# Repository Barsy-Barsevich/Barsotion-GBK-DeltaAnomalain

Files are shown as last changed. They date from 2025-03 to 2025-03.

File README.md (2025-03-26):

# Barsotion GBK DeltaAnomalain
Board computer for OKB Iva "Kilka" rocket, 2024

## Parameters
- Microcontroller: LGT8X328P
- Clock frequency: 32MHz
- Gyroscope: on-board MPU6050 (I2C)
- Barometer: external, 2x BMP388 (I2C)
- Memory: 8MB SPI NOR Flash

The clock frequency is 32 MHz provided by design, however before the flight 07.07.2024 we need to reduce it to 16 MHz, unless the computer was unstable in working.

## Software
- [DeltaAnomalain flight software](https://github.com/Barsy-Barsevich/KILKA_Soft)

## Continious progress
- [Previous version: Barsotion GBK GammaAnomalain](https://github.com/Barsy-Barsevich/Barsotion-GBK-GammaAnomalain)
- [Next version: Barsotion-EA (GBK EpsilonAnomalain](https://github.com/Barsy-Barsevich/Barsotion-EA)

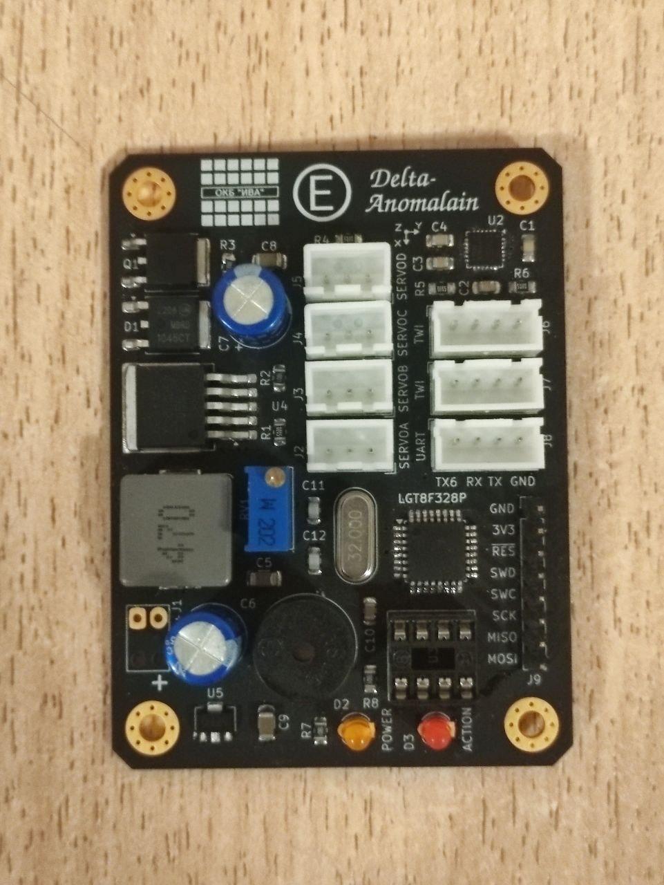
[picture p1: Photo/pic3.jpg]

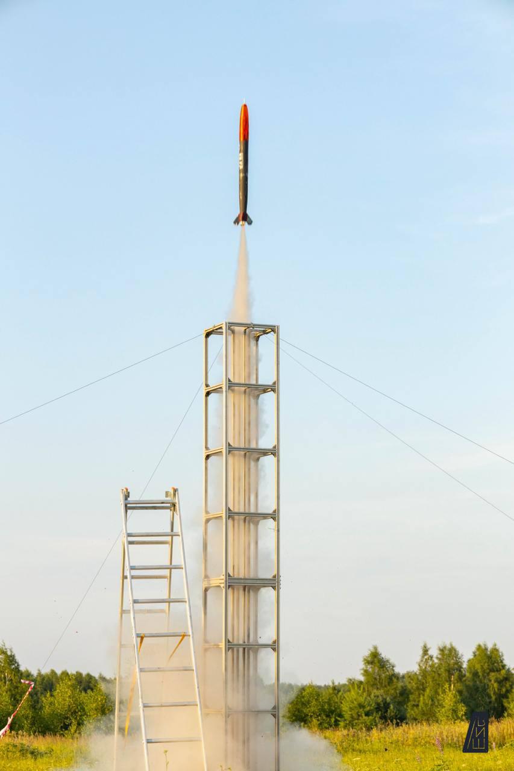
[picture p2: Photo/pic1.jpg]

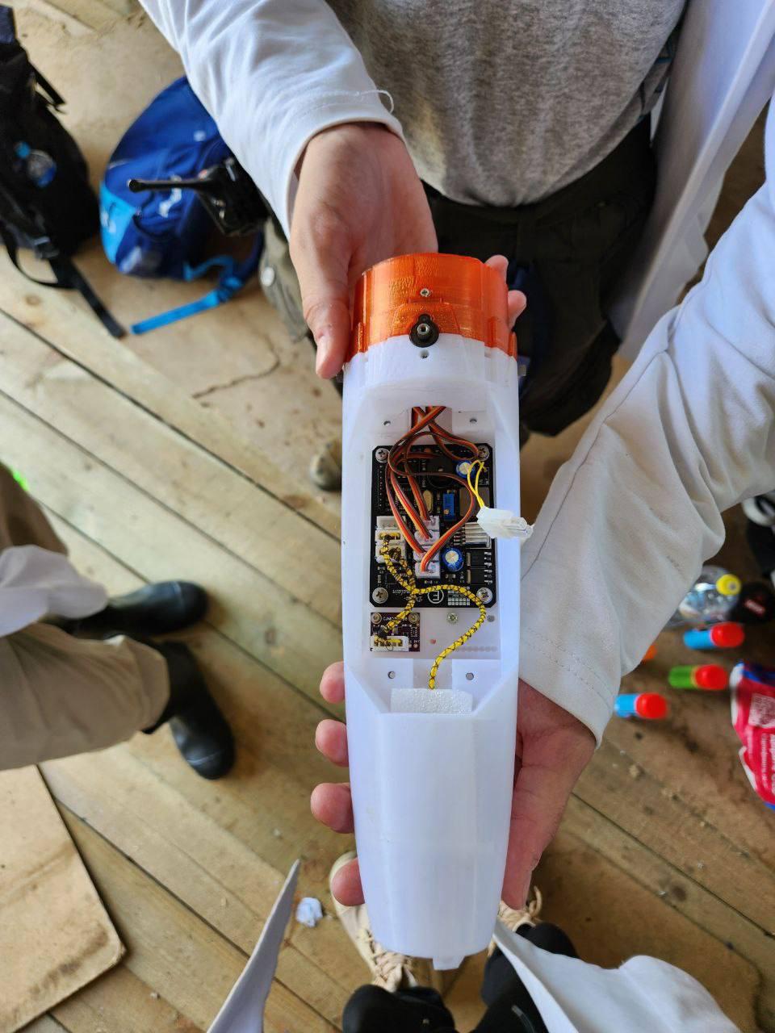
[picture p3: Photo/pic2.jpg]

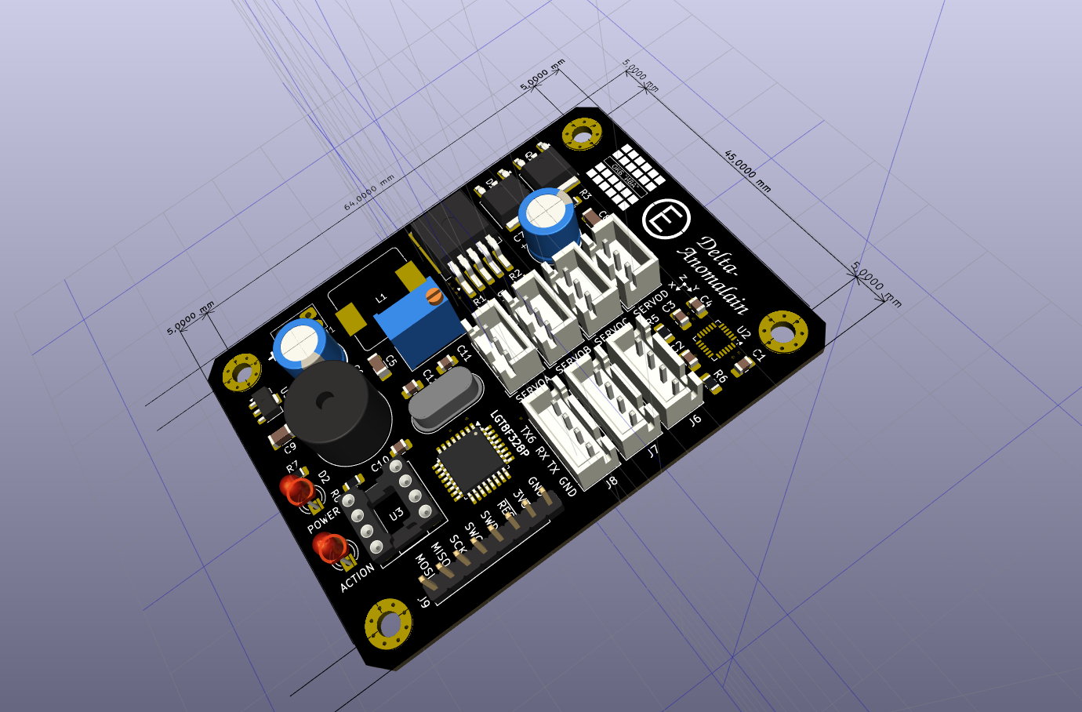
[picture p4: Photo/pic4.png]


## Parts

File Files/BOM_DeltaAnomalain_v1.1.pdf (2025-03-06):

Reference | Value | Footprint | Qty | Description
BZ1 | Buzzer | Buzzer_Beeper:MagneticBuzzer_ProSignal_ABI-009-RC | 1 Buzzer, polarized
C1 | 2.2nF | Capacitor_SMD:C_0805_2012Metric_Pad1.18x1.45mm_HandSolder | 1 Unpolarized capacitor
C2,C3 | 100nF | Capacitor_SMD:C_0805_2012Metric_Pad1.18x1.45mm_HandSolder | 2 Unpolarized capacitor
C4,C10 | 10nF | Capacitor_SMD:C_0805_2012Metric_Pad1.18x1.45mm_HandSolder | 2 Unpolarized capacitor
C5,C8,C9 | 1uF | Capacitor_SMD:C_1206_3216Metric | 3 Unpolarized capacitor
C6,C7 | 470uF | Capacitor_THT:CP_Radial_D8.0mm_P3.50mm | 2 Polarized capacitor
C11,C12 | 22pF | Capacitor_SMD:C_0805_2012Metric_Pad1.18x1.45mm_HandSolder | 2 Unpolarized capacitor
D1 | MBRD1045 | Package_TO_SOT_SMD:TO-252-2 | 1 Schottky diode, anode on pins 1 and 3
D2 | LED_Power | LED_THT:LED_D3.0mm | 1 Light emitting diode
D3 | LED_Active | LED_THT:LED_D3.0mm | 1 Light emitting diode
J1 | Power | CustomConnectors:Battery_3V7_Cable_solding_connctor | 1 Generic connector, single row, 01x02, script generated
J2 | SERVOA | Connector_JST:JST_XH_B3B-XH-A_1x03_P2.50mm_Vertical | 1 Generic connector, single row, 01x03, script generated
J3 | SERVOB | Connector_JST:JST_XH_B3B-XH-A_1x03_P2.50mm_Vertical | 1 Generic connector, single row, 01x03, script generated
J4 | SERVOC | Connector_JST:JST_XH_B3B-XH-A_1x03_P2.50mm_Vertical | 1 Generic connector, single row, 01x03, script generated
J5 | SERVOD | Connector_JST:JST_XH_B3B-XH-A_1x03_P2.50mm_Vertical | 1 Generic connector, single row, 01x03, script generated
J6 | BMP0 | Connector_JST:JST_XH_B4B-XH-A_1x04_P2.50mm_Vertical | 1 Generic connector, single row, 01x04, script generated
J7 | BMP1 | Connector_JST:JST_XH_B4B-XH-A_1x04_P2.50mm_Vertical | 1 Generic connector, single row, 01x04, script generated
J8 | UART | Connector_JST:JST_XH_B4B-XH-A_1x04_P2.50mm_Vertical | 1 Generic connector, single row, 01x04, script generated
J9 | Prog | Connector_PinHeader_2.54mm:PinHeader_1x08_P2.54mm_Vertical | 1 Generic connector, single row, 01x08, script generated
L1 | 47uH | Inductor_SMD:L_Bourns_SRP1245A | 1 Inductor with ferrite core, small symbol
Q1 | IRLR8726 | Package_TO_SOT_SMD:TO-252-2 | 1 35A Id, 60V Vds, N-Channel Power MOSFET, 18mOhm Ron, 19.3nC Qg (typ), TO252
R1 | 5.1k | Resistor_SMD:R_0805_2012Metric_Pad1.20x1.40mm_HandSolder | 1 Resistor
R2,R3,R7,R8 | 1.8k | Resistor_SMD:R_0805_2012Metric_Pad1.20x1.40mm_HandSolder | 4 Resistor
R4,R5,R6 | 10k | Resistor_SMD:R_0805_2012Metric_Pad1.20x1.40mm_HandSolder | 3 Resistor
RV1 | 2k | Potentiometer_THT:Potentiometer_Bourns_3296W_Vertical | 1 Potentiometer
U1 | LGT8F328P | Package_QFP:LQFP-32_7x7mm_P0.8mm | 1
U2 | MPU6050 | Sensor_Motion:InvenSense_QFN-24_4x4mm_P0.5mm | 1 InvenSense 6-Axis Motion Sensor, Gyroscope, Accelerometer, I2C
U3 | W25Q64FV | Package_DIP:DIP-8_W7.62mm_Socket_LongPads | 1 128Mb Serial Flash Memory, Standard/Dual/Quad SPI, SOIC-8
U4 | XL6019 | Package_TO_SOT_SMD:TO-263-5_TabPin3 | 1
U5 | LD2981_SOT89 | Package_TO_SOT_SMD:SOT-89-3 | 1 Positive 100mA 30V Linear Regulator, Fixed Output 3.3V, SOT-89
Y1 | 32 MHz | Crystal:Crystal_HC49-4H_Vertical | 1 Two pin crystal

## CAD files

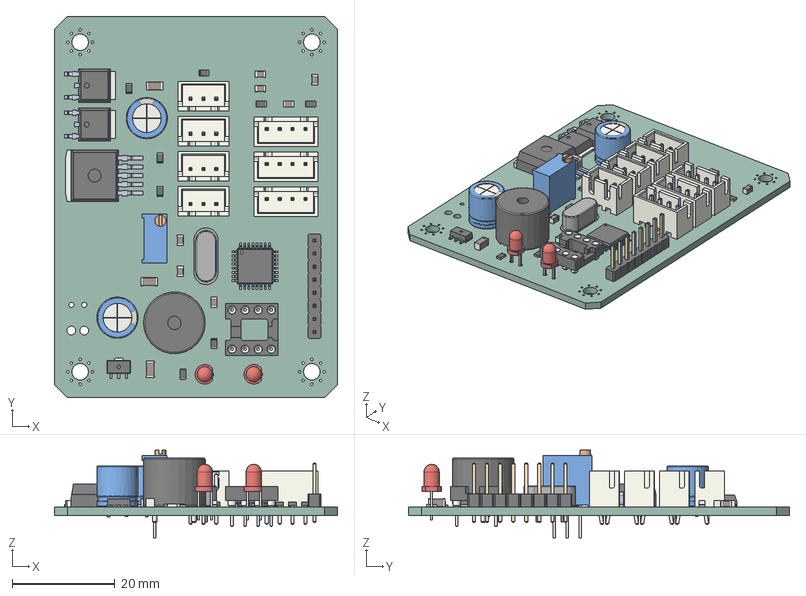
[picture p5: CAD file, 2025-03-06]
Step/DeltaAnomalain_v1.1.step
55.0 x 74.0 x 17.1 mm
CP_Radial_D80mm_P350mm x 2
PinHeader_1x08_P254mm_Vertical
R_0805_2012Metric x 8
JST_B4B_XH_A x 3
LED_D3.0mm x 2
Crystal_HC49-4H_Vertical
C_0805_2012Metric x 7
CQ assembly x 4
JST_B3B_XH_A x 4
C_1206_3216Metric x 3
DIP_8_W762mm_Socket
MagneticBuzzer_ProSignal_ABI_009_RC
Potentiometer_Bourns_3296W_Vertical
LQFP_32_7x7mm_P08mm
DeltaAnomalain_PCB

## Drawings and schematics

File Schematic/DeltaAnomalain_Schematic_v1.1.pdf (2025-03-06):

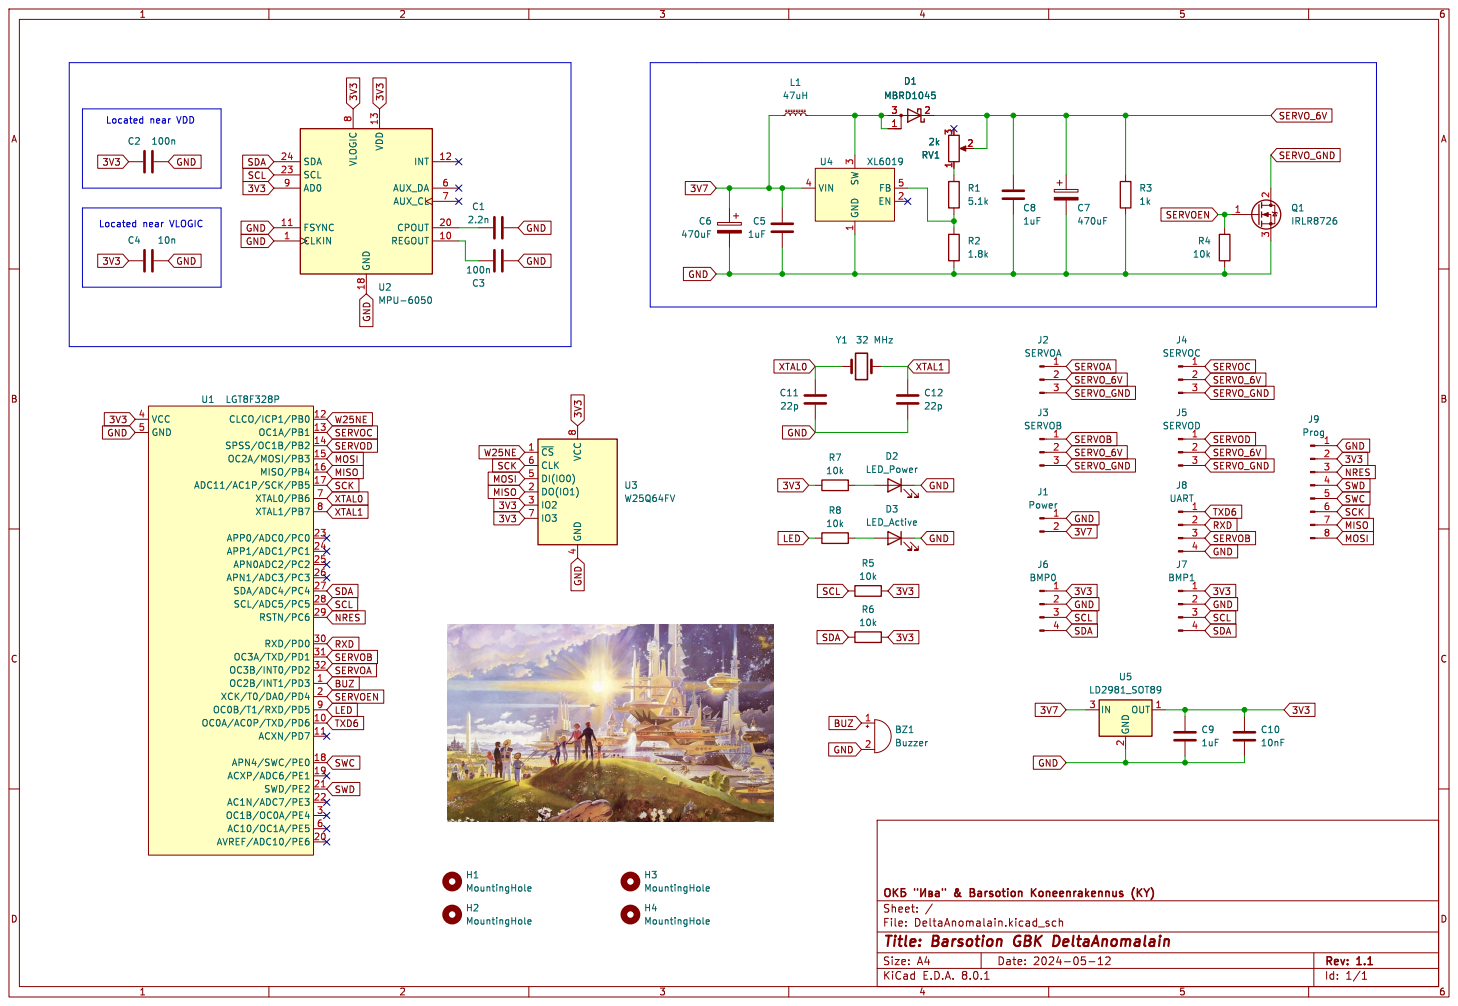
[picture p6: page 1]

Id: 1/1 Title: Barsotion GBK DeltaAnomalain

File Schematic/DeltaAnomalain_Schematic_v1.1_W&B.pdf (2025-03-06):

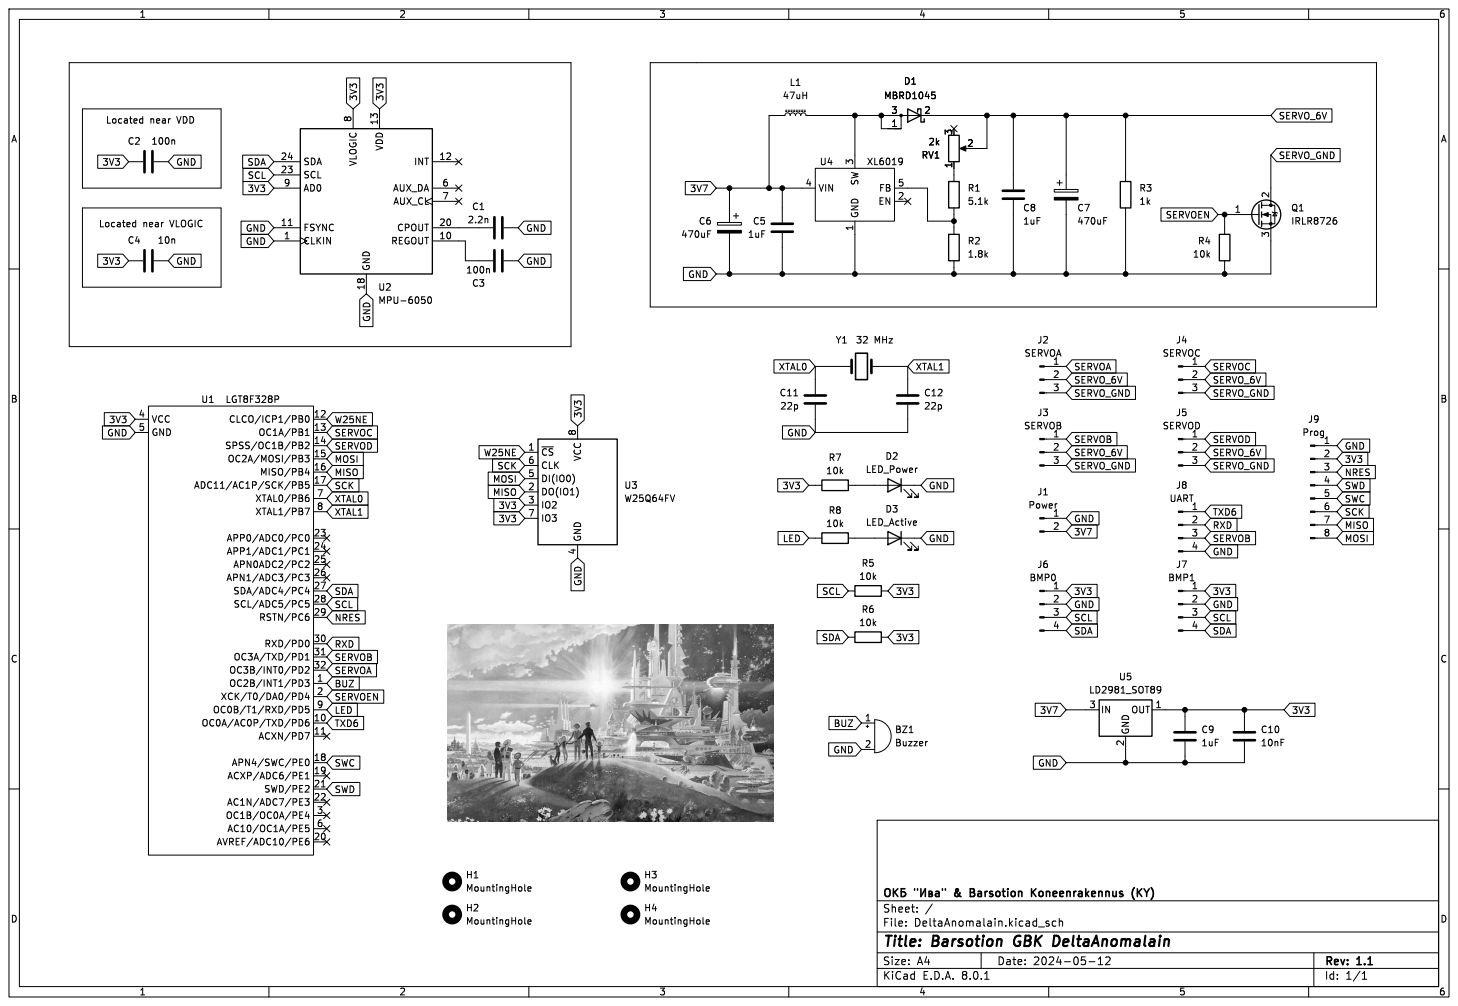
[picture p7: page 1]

Id: 1/1 Title: Barsotion GBK DeltaAnomalain

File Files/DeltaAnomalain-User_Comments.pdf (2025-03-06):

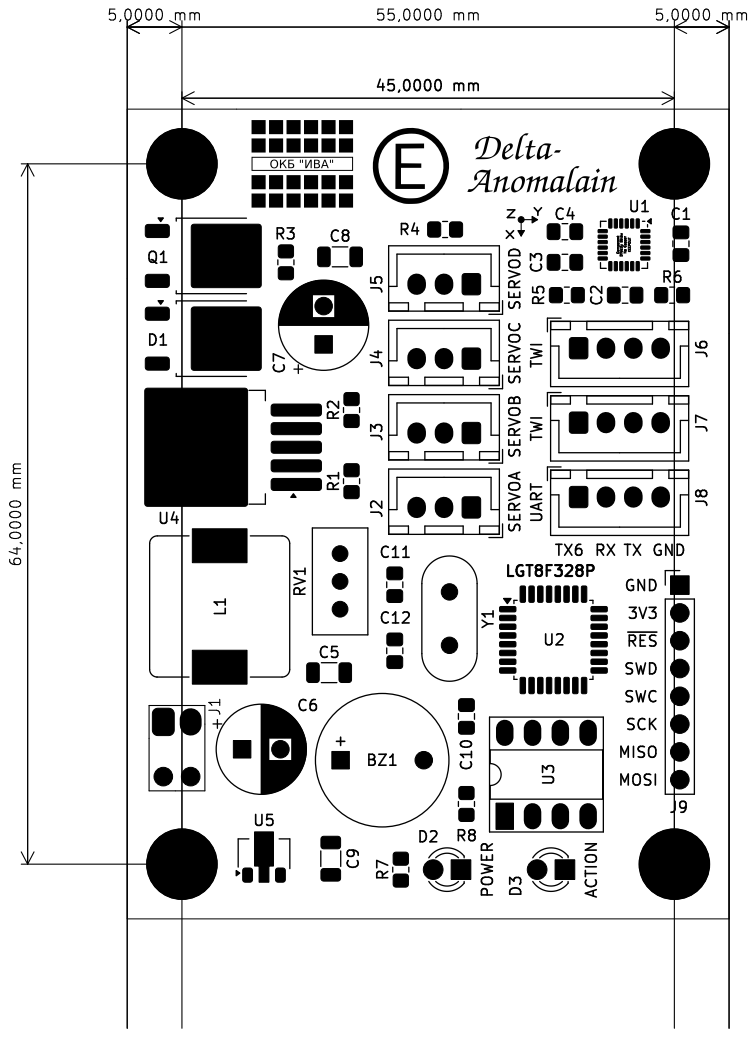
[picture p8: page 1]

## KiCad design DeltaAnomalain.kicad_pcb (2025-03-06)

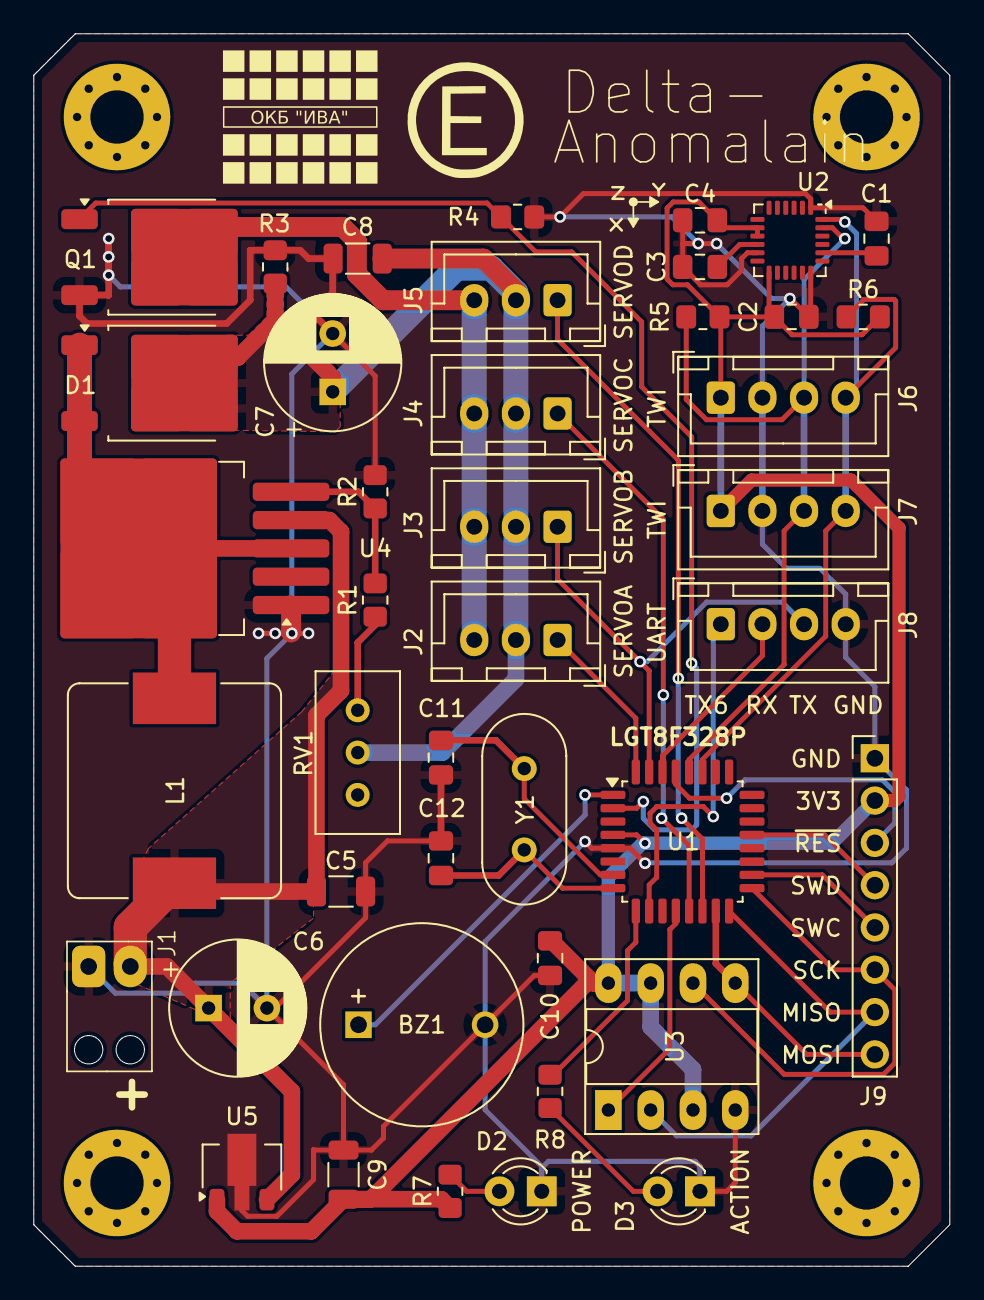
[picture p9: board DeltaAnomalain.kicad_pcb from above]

Board: 2 copper layers, 55.0 x 74.0 mm, 46 parts (0 on the bottom side), 32 nets.

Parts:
BZ1: Buzzer; MagneticBuzzer_ProSignal_ABI-009-RC
C1: 2.2n; C_0805_2012Metric_Pad1.18x1.45mm_HandSolder
C2, C3, C4: 100n; C_0805_2012Metric_Pad1.18x1.45mm_HandSolder
C5, C8, C9: 1uF; C_1206_3216Metric
C6, C7: 470uF; CP_Radial_D8.0mm_P3.50mm
C10: 10nF; C_0805_2012Metric_Pad1.18x1.45mm_HandSolder
C11, C12: 22p; C_0805_2012Metric_Pad1.18x1.45mm_HandSolder
D1: MBRD1045; TO-252-2
D2: LED_Power; LED_D3.0mm
D3: LED_Active; LED_D3.0mm
H1, H2, H3, H4: MountingHole; MountingHole_3.2mm_M3_Pad_Via
J1: Power; Battery_3V7_Cable_solding_connctor
J2: SERVOA; JST_XH_B3B-XH-A_1x03_P2.50mm_Vertical
J3: SERVOB; JST_XH_B3B-XH-A_1x03_P2.50mm_Vertical
J4: SERVOC; JST_XH_B3B-XH-A_1x03_P2.50mm_Vertical
J5: SERVOD; JST_XH_B3B-XH-A_1x03_P2.50mm_Vertical
J6: BMP0; JST_XH_B4B-XH-A_1x04_P2.50mm_Vertical
J7: BMP1; JST_XH_B4B-XH-A_1x04_P2.50mm_Vertical
J8: UART; JST_XH_B4B-XH-A_1x04_P2.50mm_Vertical
J9: Prog; PinHeader_1x08_P2.54mm_Vertical
L1: 47uH; L_Bourns_SRP1245A
Q1: IRLR8726; TO-252-2
R1: 5.1k; R_0805_2012Metric_Pad1.20x1.40mm_HandSolder
R2: 1.8k; R_0805_2012Metric_Pad1.20x1.40mm_HandSolder
R3: 1k; R_0805_2012Metric_Pad1.20x1.40mm_HandSolder
R4, R5, R6, R7, R8: 10k; R_0805_2012Metric_Pad1.20x1.40mm_HandSolder
RV1: 2k; Potentiometer_Bourns_3296W_Vertical
U1: LGT8F328P; LQFP-32_7x7mm_P0.8mm
U2: MPU-6050; InvenSense_QFN-24_4x4mm_P0.5mm
U3: W25Q64FV; DIP-8_W7.62mm_Socket_LongPads
U4: XL6019; TO-263-5_TabPin3
U5: LD2981_SOT89; SOT-89-3
Y1: 32 MHz; Crystal_HC49-4H_Vertical

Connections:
3V3: C2.1, C4.1, C9.1, C10.1, J6.1, J7.1, J9.2, R5.2, R6.2, R7.1, U1.4 (VCC), U2.8 (VLOGIC), U2.9 (AD0), U2.13 (VDD), U3.3 (IO2), U3.7 (IO3), U3.8 (VCC), U5.1 (OUT)
3V7: C5.1, C6.1, J1.2, L1.1, U4.4 (VIN), U5.3 (IN)
BUZ: BZ1.1 (+), U1.1 (OC2B/INT1/PD3)
GND: BZ1.2 (-), C1.2, C2.2, C3.2, C4.2, C5.2, C6.2, C7.2, C8.2, C9.2, C10.2, C11.2, C12.2, D2.1 (K), D3.1 (K), J1.1, J6.2, J7.2, J8.4, J9.1, Q1.3 (S), R2.2, R3.2, R4.2, U1.5 (GND), U2.1 (CLKIN), U2.11 (FSYNC), U2.18 (GND), U3.4 (GND), U4.1 (GND), U5.2 (GND)
LED: R8.1, U1.9 (OC0B/T1/RXD/PD5)
MISO: J9.7, U1.16 (MISO/PB4), U3.2 (DO(IO1))
MOSI: J9.8, U1.15 (OC2A/MOSI/PB3), U3.5 (DI(IO0))
NRES: J9.3, U1.29 (RSTN/PC6)
unnamed: D2.2 (A), R7.2
unnamed: D3.2 (A), R8.2
unnamed: R1.1, RV1.1
unnamed: C1.1, U2.20 (CPOUT)
unnamed: C3.1, U2.10 (REGOUT)
unnamed: R1.2, R2.1, U4.5 (FB)
unnamed: D1.1 (A), D1.3 (A), L1.2, U4.3 (SW)
RXD: J8.2, U1.30 (RXD/PD0)
SCK: J9.6, U1.17 (ADC11/AC1P/SCK/PB5), U3.6 (CLK)
SCL: J6.3, J7.3, R5.1, U1.28 (SCL/ADC5/PC5), U2.23 (SCL)
SDA: J6.4, J7.4, R6.1, U1.27 (SDA/ADC4/PC4), U2.24 (SDA)
SERVOA: J2.1, U1.32 (OC3B/INT0/PD2)
SERVOB: J3.1, J8.3, U1.31 (OC3A/TXD/PD1)
SERVOC: J4.1, U1.13 (OC1A/PB1)
SERVOD: J5.1, U1.14 (SPSS/OC1B/PB2)
SERVOEN: Q1.1 (G), R4.1, U1.2 (XCK/T0/DA0/PD4)
SERVO_6V: C7.1, C8.1, D1.2 (K), J2.2, J3.2, J4.2, J5.2, R3.1, RV1.2
SERVO_GND: J2.3, J3.3, J4.3, J5.3, Q1.2 (D)
SWC: J9.5, U1.18 (APN4/SWC/PE0)
SWD: J9.4, U1.21 (SWD/PE2)
TXD6: J8.1, U1.10 (OC0A/AC0P/TXD/PD6)
W25NE: U1.12 (CLCO/ICP1/PB0), U3.1 (~CS)
XTAL0: C11.1, U1.7 (XTAL0/PB6), Y1.1
XTAL1: C12.1, U1.8 (XTAL1/PB7), Y1.2
